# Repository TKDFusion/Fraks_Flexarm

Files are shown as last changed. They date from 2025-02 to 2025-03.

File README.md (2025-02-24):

# FRAKS Flexarm

Fraks Flexarm

### Free Range Arm Kinematics System

The Fraks Flexarm is a tool-balancing arm designed to keep the attached tool parallel throughout its movement. It was created to hold soldering irons to install heat set inserts into 3D printed parts.

It has a large working area for its size, and has quick release tool holders that are held in place with magnets.

Thanks to Zack Freedman for making Gridfinity an open source project, I have included Gridfinity storage into the base. You can read more about Gridfinity at <https://gridfinity.xyz/>

Fraks Animation

___

# What do I need?

* You will also need either pocket screws or a wood working fence clamp to secure the base to your work surface.

* 4 pieces of 1515 extrusion, all cut to the same length and tapped on either end. I have tested this with 200mm and 270mm lengths.

* 10x1x60mm extension springs, these seem to work well for 200-300mm builds. You can adjust the tension rate by moving the spring posts along the 1515 extrusion.

* 10x100mm dowel pin and a 10x14x30mm brass Bushing

* M10 washer, a 25mm diameter is listed, but any diameter and thickness washer will work.

* M5x30 FHCS are recommended, but BHCS are also supported. The springs will touch button heads slightly, but will not affect performance from testing.

* You will need a Soldering iron with a heatset insert adapter. I personally recommend either the Pinecil or TS101 Soldering Irons along with the adapter set from CNC Kitchen.

| **Current Supported Irons:** | |
|---|---|
| **Pinecil** with CNC Kitchen TS100&TS101 Adapter Set |Pinecil |
| **TS101** with CNC Kitchen TS100&TS101 Adapter Set |PTS101 |
| Imported adjustable solder iron (Generic) |China_Soldering_iron |

___

## BOM

| Part Description | Quantity | |
|---|---|---|
| 1515 Extrusion 200-300mm (All the same length) | 4 |1515_Extrusion |
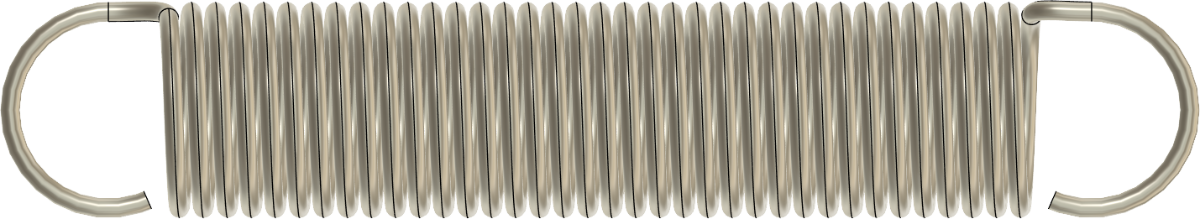
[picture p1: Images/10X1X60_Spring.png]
10X1X60_Spring
| 10mm OD x 1mm Wire Gauge x 60mm Long Extension Springs | 4 | |
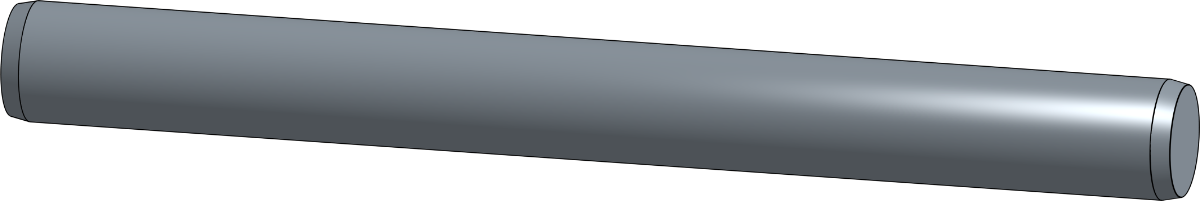
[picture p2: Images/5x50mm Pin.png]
Pin
| 10mm x 100mm long Pin | 1 | |
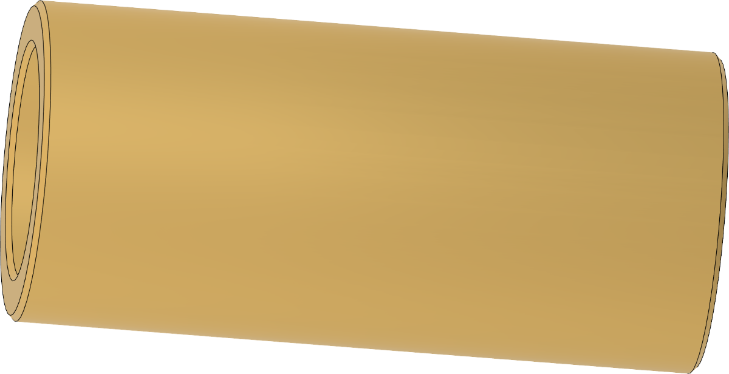
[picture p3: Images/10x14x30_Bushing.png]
10x14x30_Bushing
| 10mm ID x 14mm OD x 30mm Length Brass Bushing | 1 | |
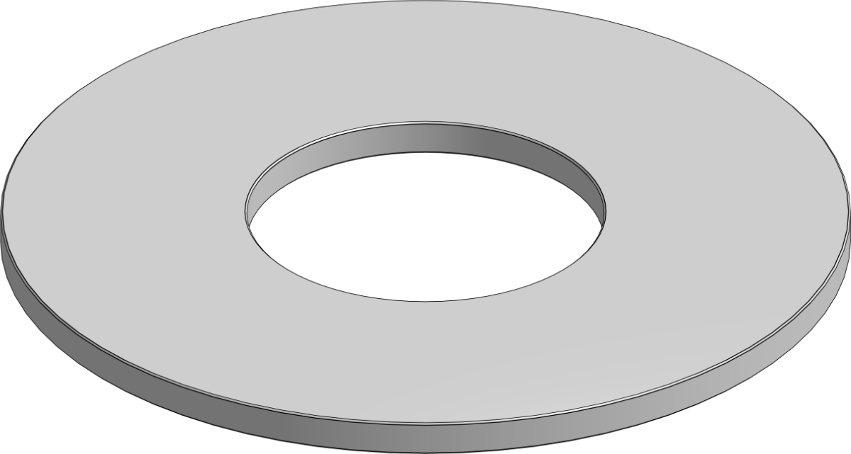
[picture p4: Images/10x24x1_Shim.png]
10x24x1_Shim
| 10mmx24mm Washer | 1 | |
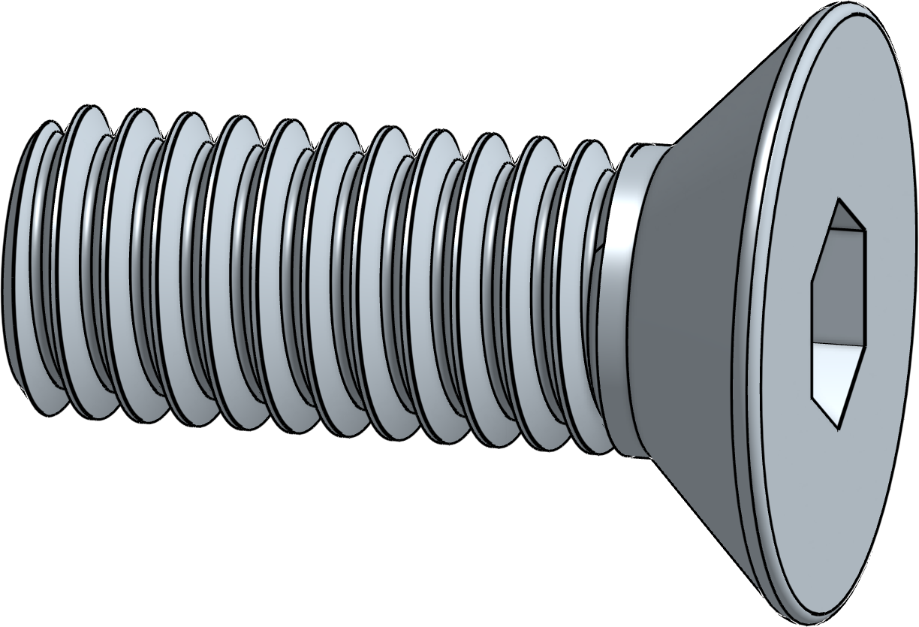
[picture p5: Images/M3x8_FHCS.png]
M3x8_FHCS
| M3x8 FHCS | 16 | |
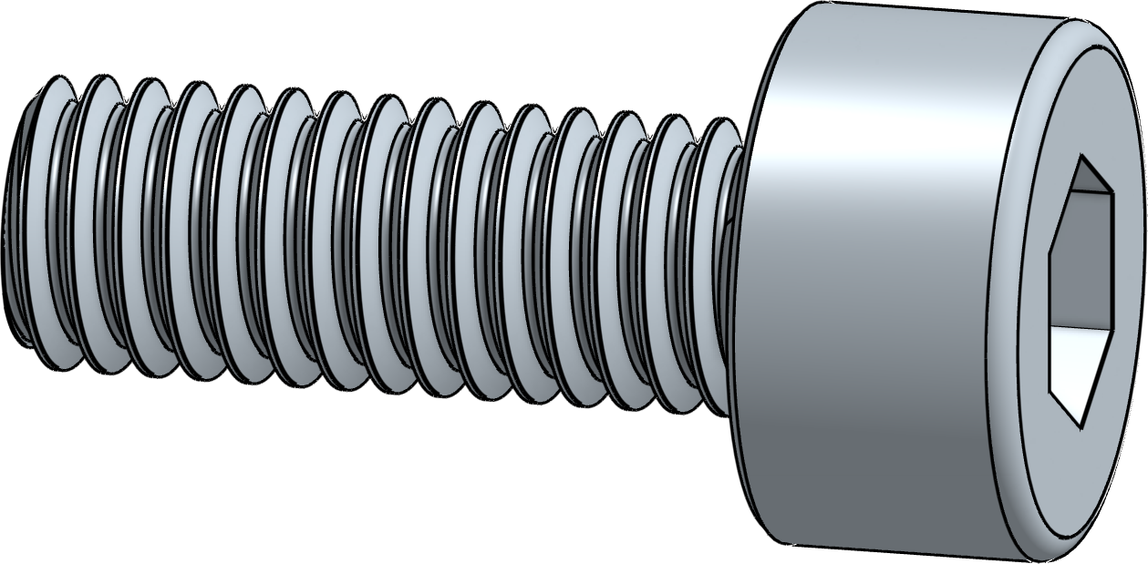
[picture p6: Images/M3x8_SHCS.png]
M3x8_SHCS
| M3x8 SHCS | 10 | |
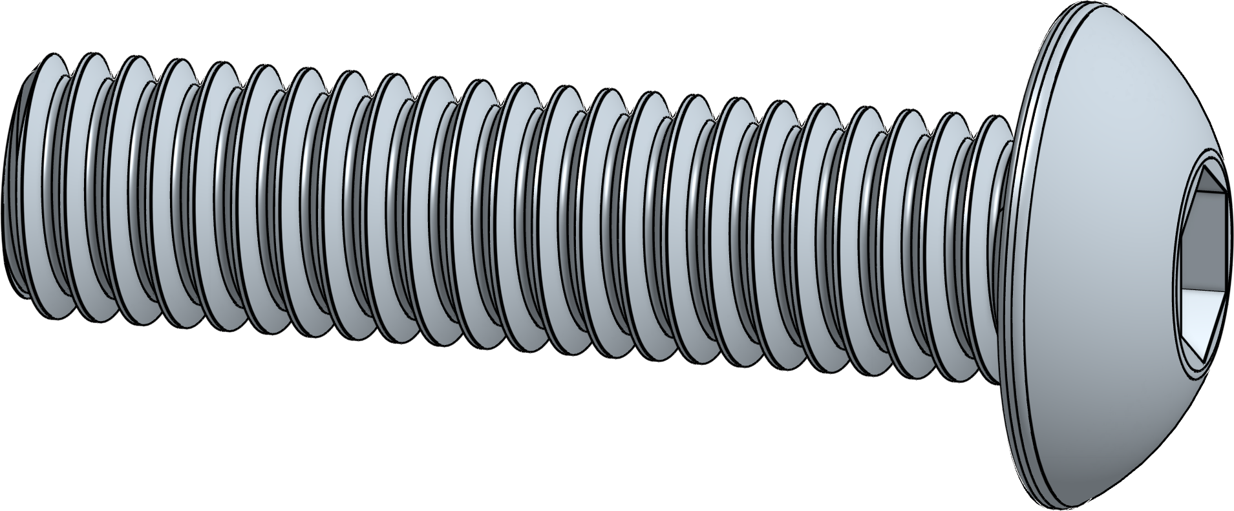
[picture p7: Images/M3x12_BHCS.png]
M3x12_BHCS
| M3x12 BHCS | 4 | |
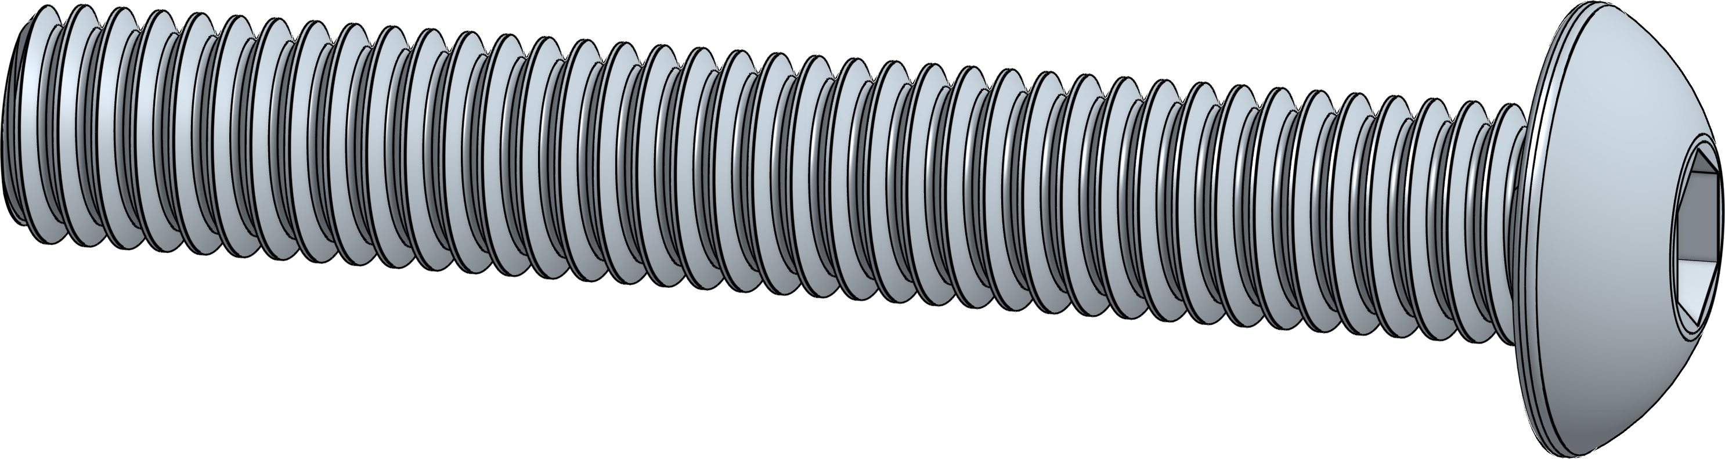
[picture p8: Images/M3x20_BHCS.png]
M3x20_BHCS
| M3x20 BHCS | 4 | |
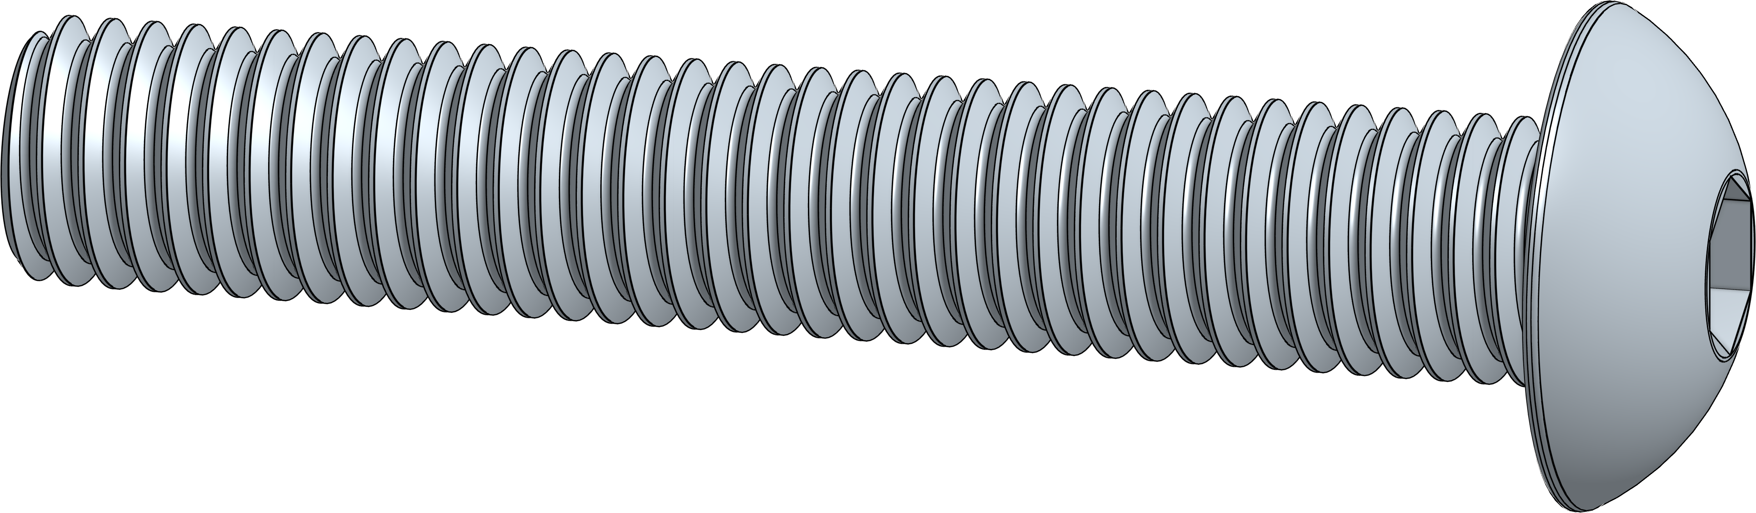
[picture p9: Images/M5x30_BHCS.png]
M5x30_BHCS
| M5x30 FHCS (Or BHCS) | 8 | |
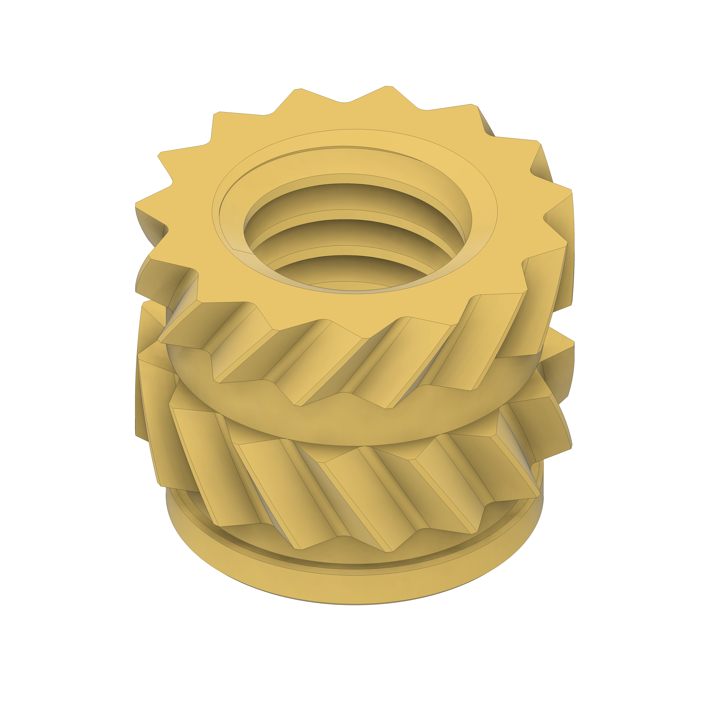
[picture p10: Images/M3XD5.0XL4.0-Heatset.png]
M3 Heatset
| M3 Heatset Inserts (5mm OD x 4mm Length) | 10 | |
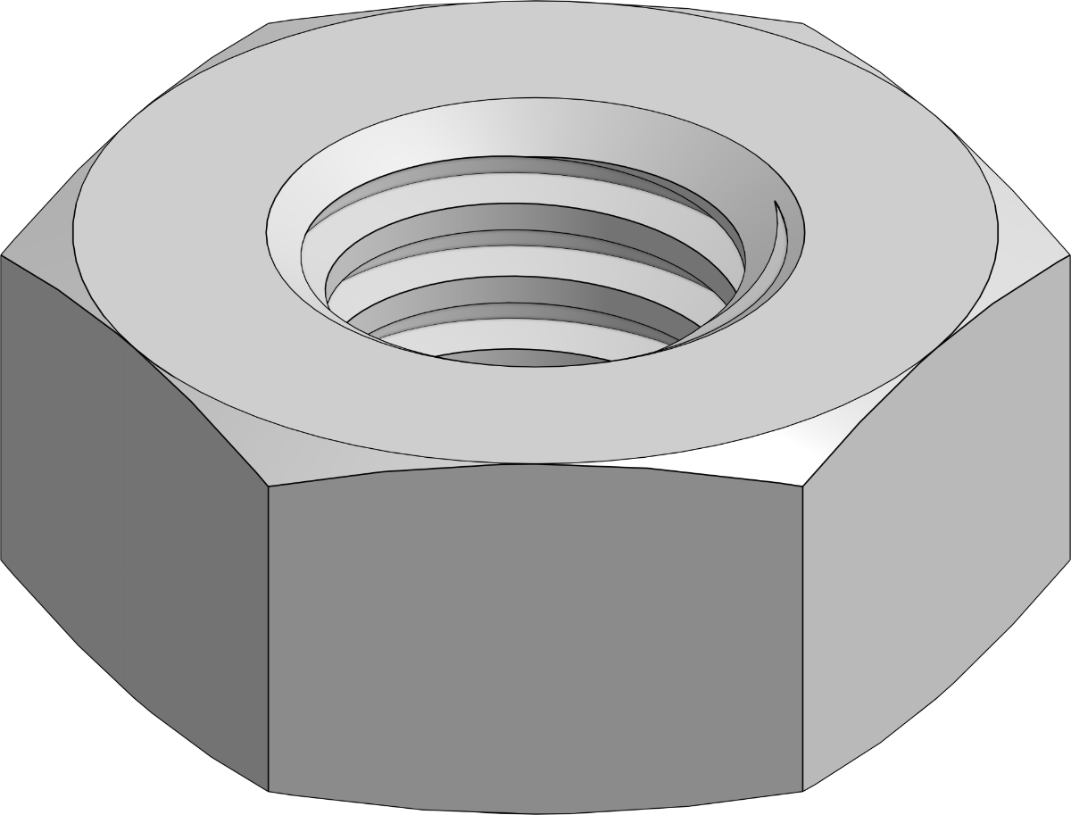
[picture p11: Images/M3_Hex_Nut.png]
M3_Hex_Nut
| M3 Hex Nuts | 20 | |
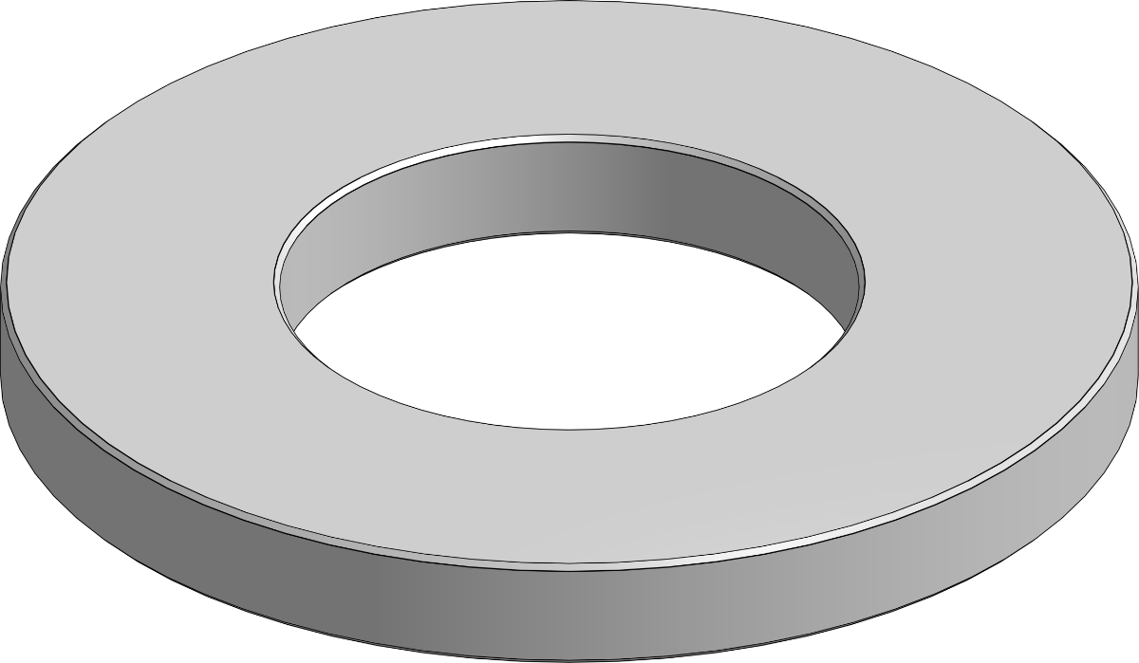
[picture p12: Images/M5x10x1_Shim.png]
M5x10x1_Shim
| M5 Washers/Shims (10x1) | 16 | |
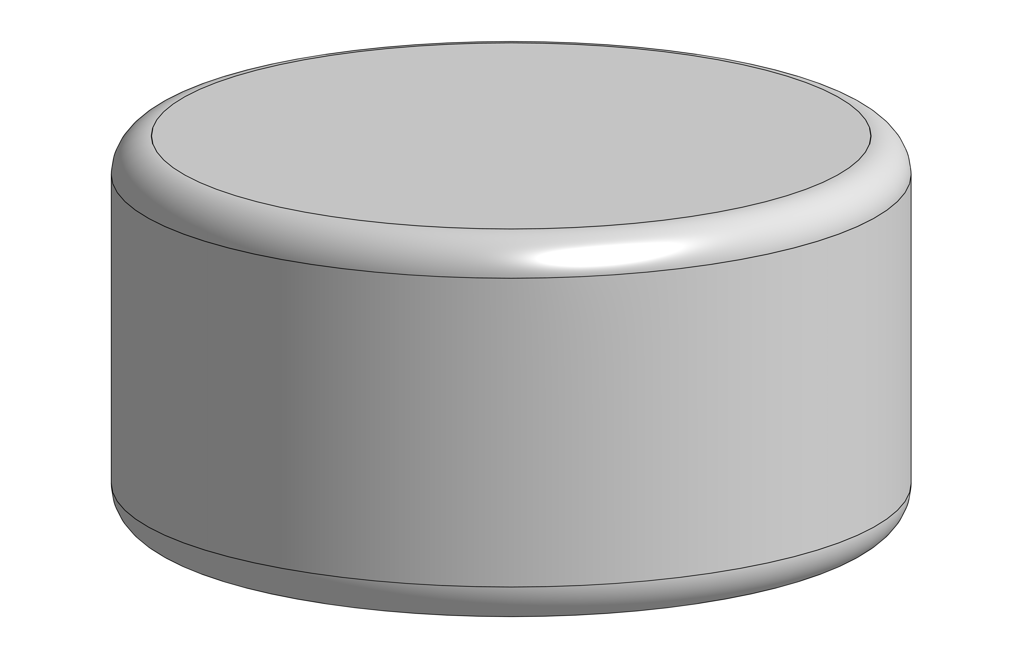
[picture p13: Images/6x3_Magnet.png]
6x3_Magnet
| 6x3 Magnets | 6 | |
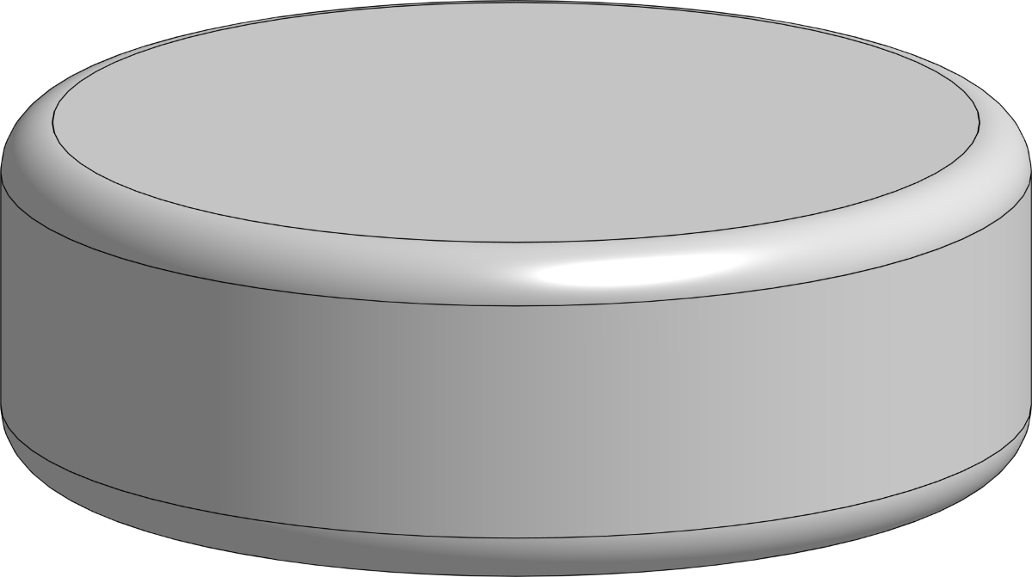
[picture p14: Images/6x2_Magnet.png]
6x2_Magnet
| 6x2 Magnets (For Gridfinity Base) | 12 | |
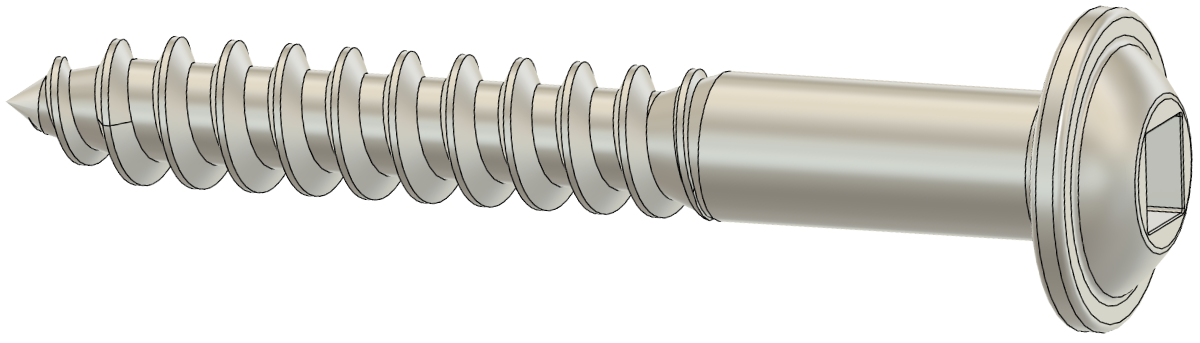
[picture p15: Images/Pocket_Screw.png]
Pocket_Screw
| 1-1/4 #8 Pocket screws (For screwing base to table) | 4 | |
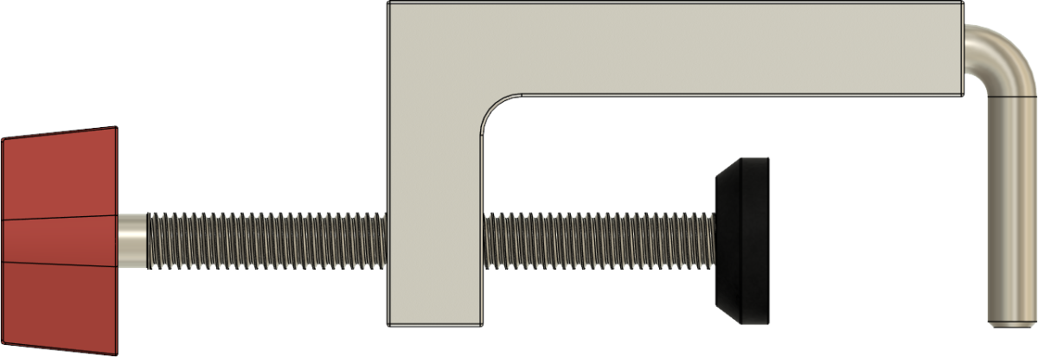
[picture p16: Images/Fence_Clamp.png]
Fence_Clamp
| Table Saw Fence Clamp (For clamping to table) | 1 | |

___

## Amazon links

[Fence Clamps](https://www.amazon.com/gp/product/B07CJHZ7QL/ref=ox_sc_act_title_2?smid=ATVPDKIKX0DER&th=1)

[10x1x60 Springs](https://www.amazon.com/gp/product/B0CJFFL9MW)

[10x14x30 Bushing](https://www.amazon.com/gp/product/B09QYQS7RX)

<br>

## Vendor Kits

[DLL-PDF](https://dllpdf.com/fraks-flexarm) - Has extrusion kits and a M3/M5 Screw only hardware option. They offer custom powder-coating, and will cut the extrusions to any length you want.

[Fabreeko](https://www.fabreeko.com/products/fraks-flexarm-heat-insert-press-kits-by-turtle-crawler)   -
 Offers complete kits in 3 sizes, 300mm, 350mm, and 400mm. A portion of all sales from the Fabreeko listing are donated to me.

[KB-3D](https://kb-3d.com/store/tools-equipment/3474-fraks-flexarm-system-heat-set-insert-tool-configurator.html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) - Offers customizable kits that let you pick and choose exactly what you need. This is great if you already have a good assortment of hardware. They also have the TS101 Iron and CNC Kitchen tip set. This is an affiliate link, and using this link will give me a small kickback of the total order.

___

# Print Settings

* 0.2mm layer heights

* 0.4mm Line Width

* 4-5 walls

* 4-5 top and bottom layers

* 40% infill

* ABS and ASA have been tested

# Assembly Tips

___

* The center arms use a pair of magnets to pull the arms together when parked. Build 2 arms with magnets that that attract to each other.

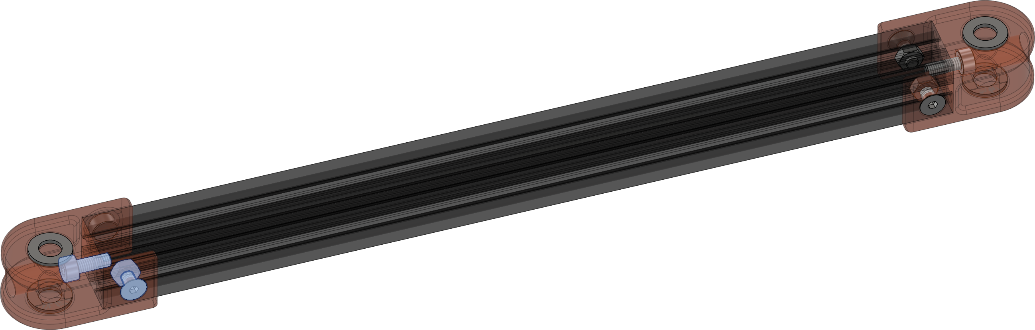
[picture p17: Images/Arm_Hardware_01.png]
Arm_Hardware_01


* Build the other 2 arms like the image bellow, with the spring standoffs placed 90mm from one end. You can adjust these later.

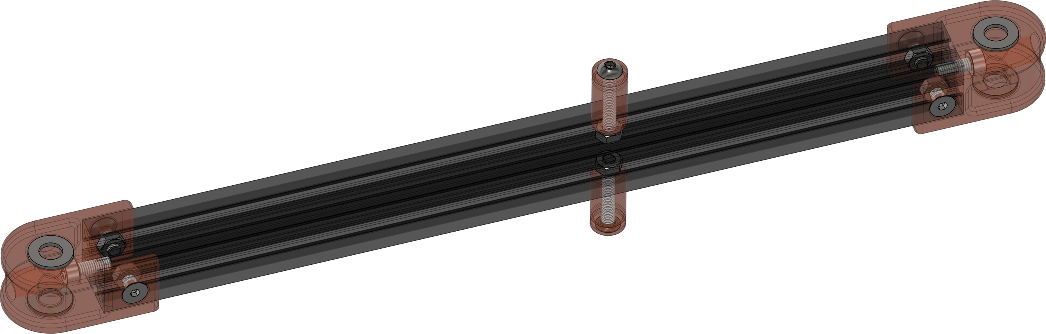
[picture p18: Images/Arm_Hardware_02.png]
Arm_Hardware_01


___

## *Refer to cad for further assembly help*

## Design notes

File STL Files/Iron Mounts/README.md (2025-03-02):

# Iron Mounts

The mounts have 3 fitment options depending on the tolerances of your printer.

* Files ending in 002 have a gap of 0.02mm
* Files ending in 010 have a gap of 0.1mm
* Files ending in 020 have a gap of 0.2mm

___

I recommend starting with 010 or just printing all 3. The mount should be a light slip fit into the front bracket, a light drag is ideal. If you have issues getting the right fit please let me know in discord or create a post in the discussions forum in the github.

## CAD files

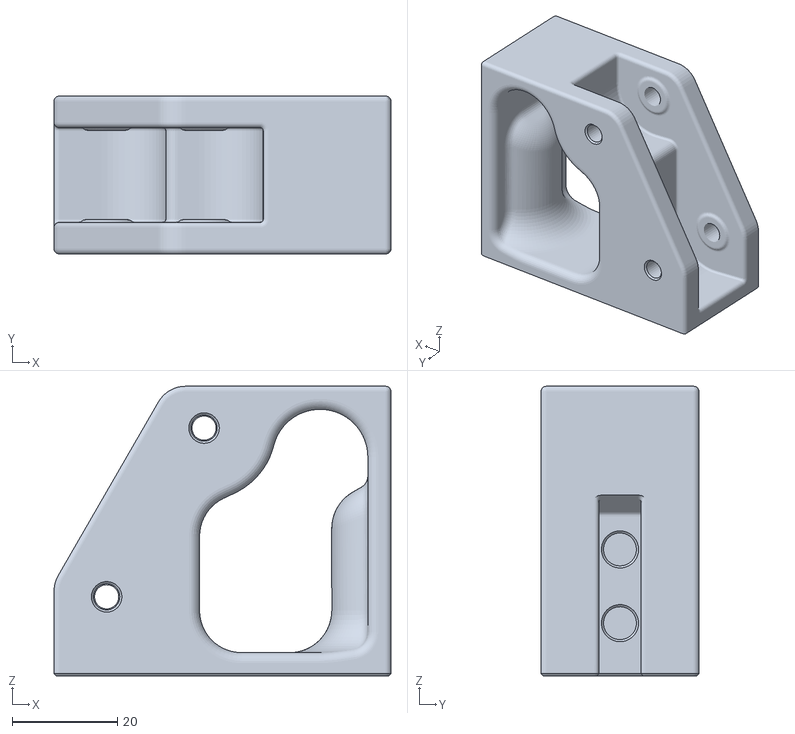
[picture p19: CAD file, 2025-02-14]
STL Files/F695_Mod/BHCS_F695_Front_Bracket.stl
64.0 x 30.0 x 55.0

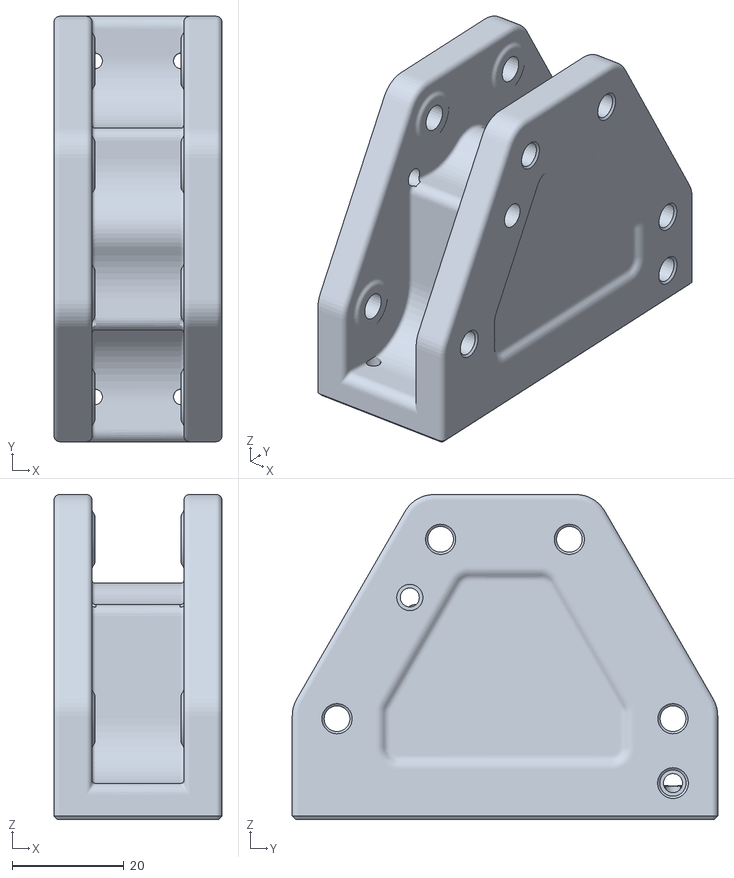
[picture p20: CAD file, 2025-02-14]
STL Files/FHCS_Center_Bracket.stl
30.0 x 76.0 x 58.0

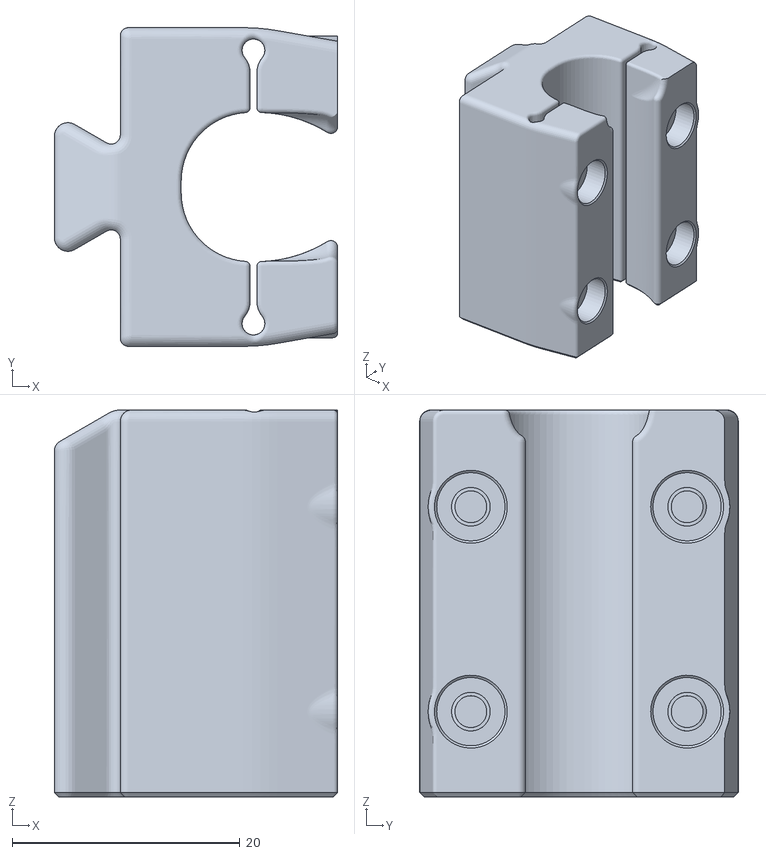
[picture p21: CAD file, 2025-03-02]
STL Files/Iron Mounts/TS101_Mount_020.stl
24.9 x 28.0 x 34.0

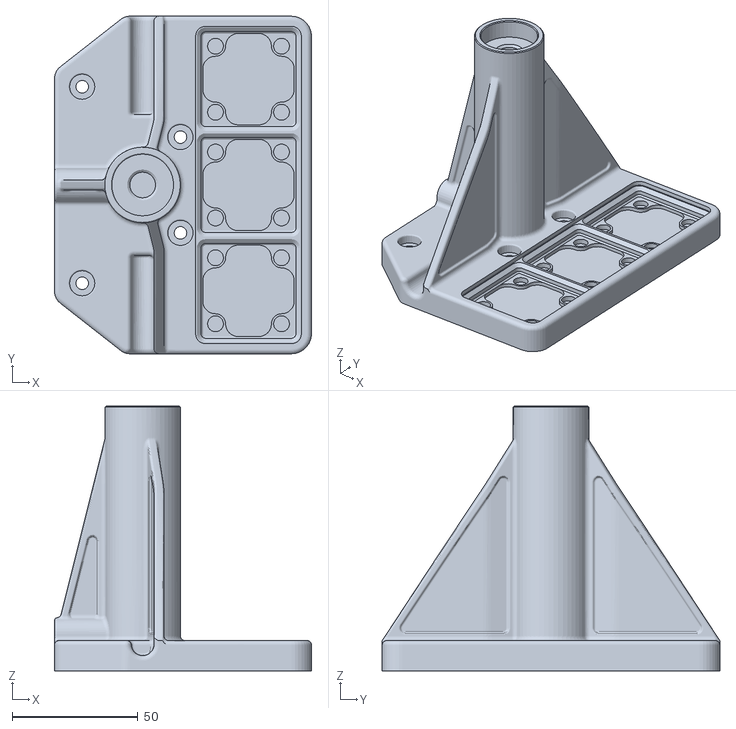
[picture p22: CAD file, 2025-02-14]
STL Files/Thrust_Bearing_Bases/Bench_Mount_Base-51100_Bearing.stl
102.0 x 134.0 x 105.0

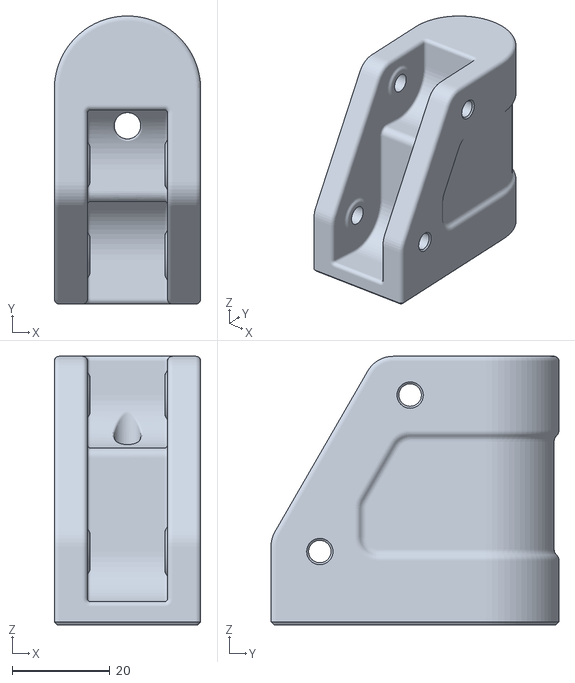
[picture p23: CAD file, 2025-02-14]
STL Files/FHCS_Rear_Bracket.stl
30.0 x 59.0 x 55.0

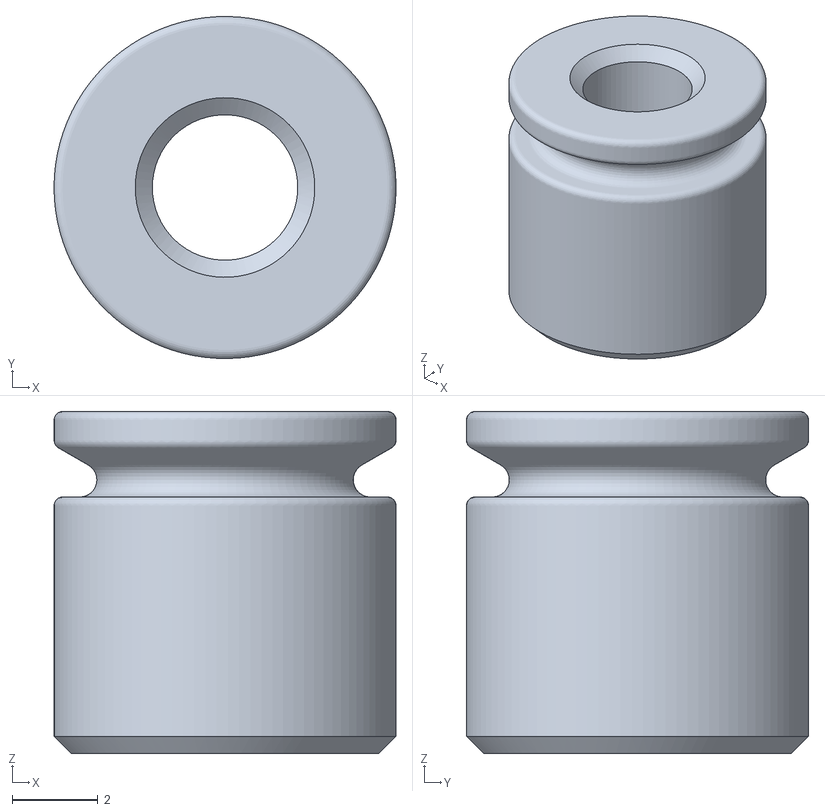
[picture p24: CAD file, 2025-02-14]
STL Files/a_Short_Spring_Retainer-x4.stl
8.00 x 8.00 x 8.00

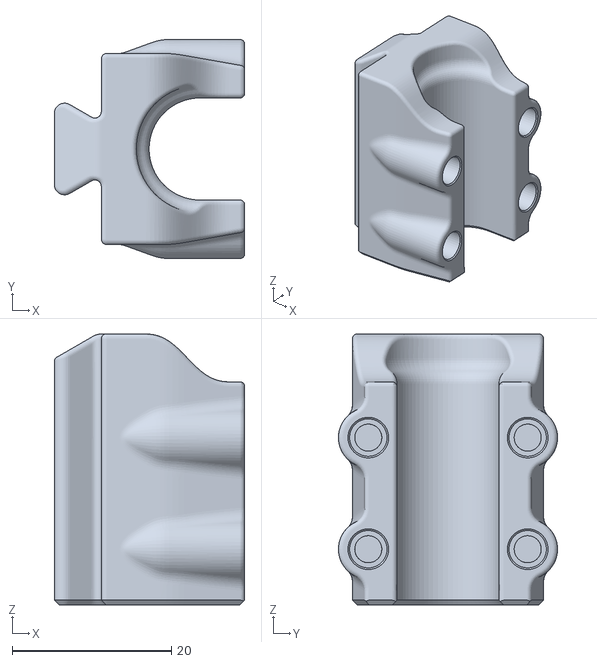
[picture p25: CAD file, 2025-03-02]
STL Files/Iron Mounts/Pinecile_Mount_010.stl
23.9 x 27.5 x 34.0

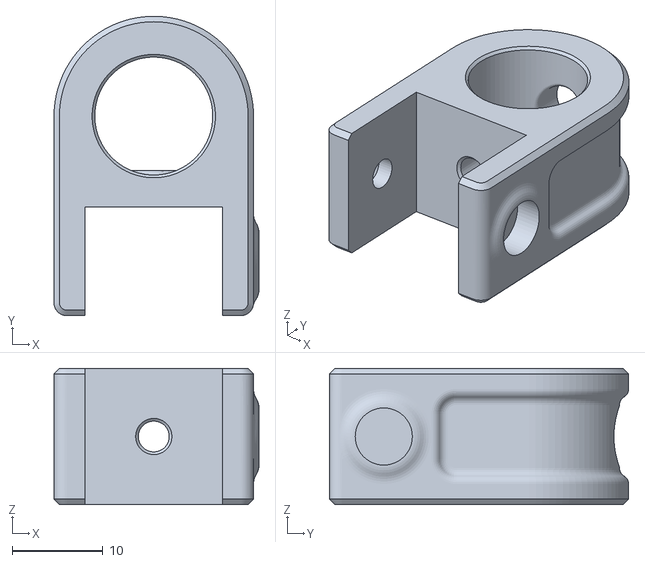
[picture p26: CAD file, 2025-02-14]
STL Files/F695_Mod/a_Joint_F695_Magnet-x2.stl
22.6 x 33.0 x 15.0

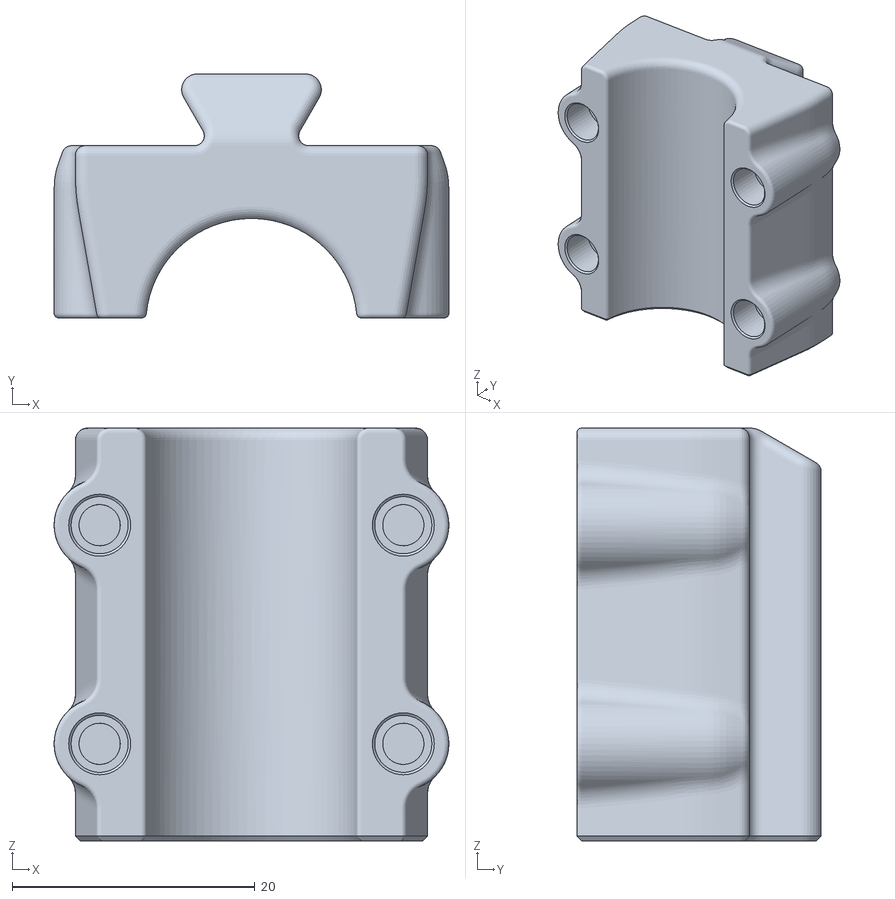
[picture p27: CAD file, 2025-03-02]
STL Files/Iron Mounts/17mm_Round_Mount_010.stl
32.5 x 20.1 x 34.0

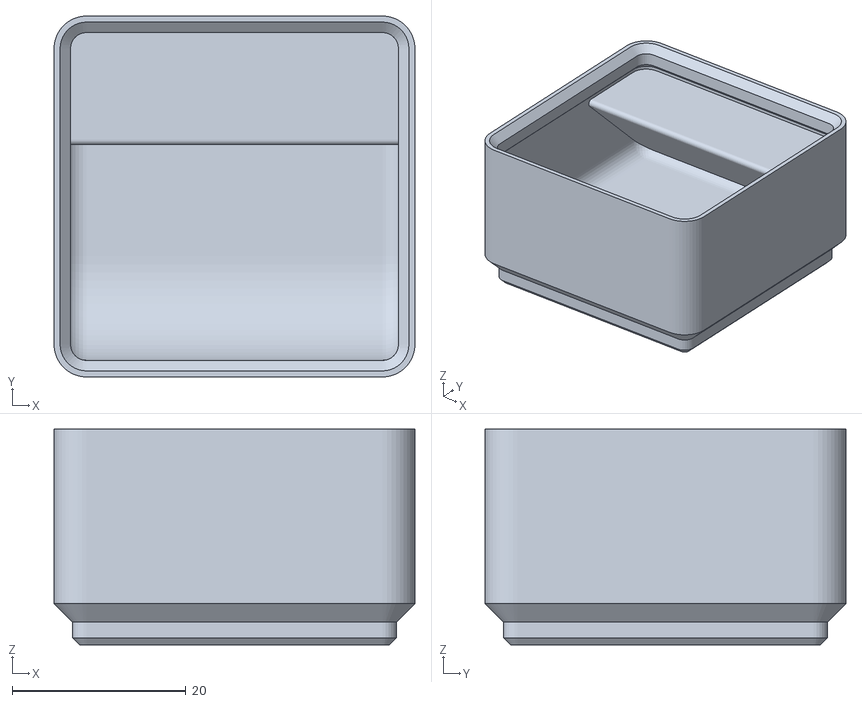
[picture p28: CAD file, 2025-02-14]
STL Files/Gridfinity bin 1x1x3.stl
41.5 x 41.5 x 24.8

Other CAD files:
STL Files/F695_Mod/FHCS_F695_Center_Bracket.stl
STL Files/Iron Mounts/TS101_Mount_010.stl
STL Files/Thrust_Bearing_Bases/Bench_Mount_Base-AXK1024_Bearing.stl
STL Files/F695_Mod/FHCS_F695_Front_Bracket.stl
STL Files/BHCS_Center Bracket.stl
STL Files/F695_Mod/BHCS_F695_Center_Bracket.stl
STL Files/Iron Mounts/17mm_Round_Mount_020.stl
STL Files/F695_Mod/FHCS_F695_Rear_Bracket.stl
STL Files/BHCS_Front_Bracket.stl
STL Files/BHCS_Rear_Bracket.stl
STL Files/Bench_Mount_Base.stl
STL Files/Cable_Mount-4mm-x4.stl
STL Files/Cable_Mount-5mm-x4.stl
STL Files/Cable_Mount-6mm-x4.stl
STL Files/Cable_Mount-Oval-4mm-x4.stl
STL Files/F695_Mod/BHCS_F695_Rear_Bracket.stl
STL Files/F695_Mod/a_Joint-F695-x6.stl
STL Files/FHCS_Front_Bracket.stl
STL Files/Front_bracket_Guard_Long.stl
STL Files/Front_bracket_Guard_Medium.stl
STL Files/Gridfinity CNCKitchen Iron Tips v1.stl
STL Files/Gridfinity bin 1x2x3.stl
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

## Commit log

2025-02-19 BOM Fix
    Corrected amount of 6x3 magnets from 2 to 6.
2025-03-02 Added Iron mount offset files
    Some users reported the iron mounts being to tight, so I have added some files with larger gaps in the dovetail feature.
    [17mm_Round_Clamp.stl, 17mm_Round_Mount_002.stl, 17mm_Round_Mount_010.stl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]
